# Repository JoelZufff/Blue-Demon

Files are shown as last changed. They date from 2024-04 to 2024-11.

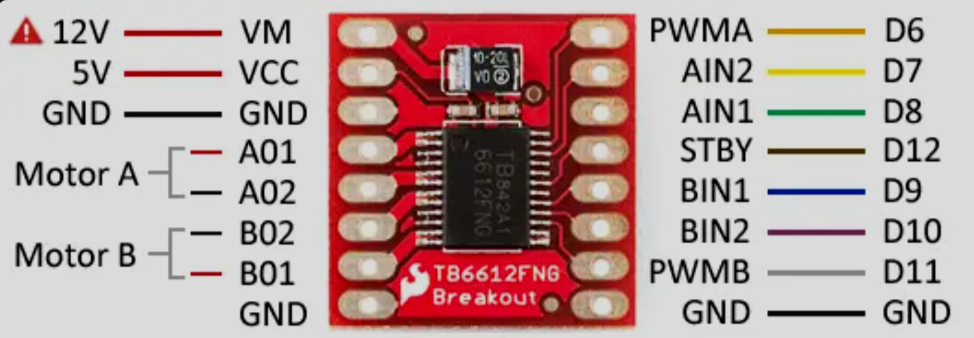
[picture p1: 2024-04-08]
Auxiliar-Files/HW-166.png

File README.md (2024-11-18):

**Robot para competencia Minisumo**
Este fue uno de mis proyectos más demandantes, ya que, además de las limitaciones de tamaño y peso de la competencia, todo se creó desde cero, sin comprar diseños preexistentes ni módulos de control preprogramados.

**Diseño:**  
Se diseñó de manera personalizada desde cero en el software SOLIDWORKS, teniendo en cuenta las restricciones de tamaño de la competencia.

- Se priorizó el máximo aprovechamiento del espacio, asegurando una distribución adecuada del peso para lograr un diseño estable.
- La carcasa fue impresa en 3D con filamento PETG de color azul. Se eligió este material por su mayor dureza en comparación con el PLA.
- La base fue fabricada en una placa de aluminio con la ayuda de un profesor, a partir de un modelo 3D.

**Programación de microcontrolador:**  
La programación se realizó utilizando PIC C COMPILER.

- Se configuraron los periféricos manipulando registros a través de punteros, obteniendo las direcciones de memoria de la hoja de datos del fabricante.
- Se implementó una codificación robusta y fácil de entender, aprovechando las herramientas del lenguaje C, como funciones selectivas, iterativas, estructuras y punteros.
- Se utilizaron **TIMERS** para generar 4 señales PWM y un timer con interrupción exclusivo para verificar la conexión con el control.
- Se empleó el protocolo de comunicación serial **RS232** para recibir las instrucciones del controlador.

**Programación de control:**  
Se desarrolló un programa en **C#** para Windows que actuó como intermediario entre el control y el robot Minisumo.

- Se aprovechó la compatibilidad del software para obtener la posición de los joysticks, botones y gatillos de un control de Xbox. Los datos obtenidos se organizaban en una cadena de caracteres siguiendo nuestro propio protocolo.
- Se utilizó un **TIMER** para enviar los datos recibidos del control a una tasa de 40 Hz. Estos datos se transmitían al microcontrolador del robot a través de Bluetooth utilizando el protocolo **RS232**.
- Los datos se enviaban a una tasa fija para que el microcontrolador pudiera detectar una desconexión cuando no se recibían datos en un periodo determinado.

**Componentes electrónicos:**  

- **Microcontrolador PIC 18F26K22**: Microcontrolador de 16 MHz con 5 módulos CCPX, lo que nos permitió generar 4 señales PWM independientes.
- **Módulo Bluetooth HC-05**: Módulo que facilitó la recepción de datos desde la computadora al microcontrolador mediante Bluetooth.
- **4 micromotorreductores de 150 rpm**: Motores con engranajes metálicos que ofrecieron un buen equilibrio entre torque y velocidad.
- **Regulador de voltaje L7805**: Acompañado de un condensador, ayudó a regular el voltaje de la batería para alimentar el microcontrolador.
- **Driver puente H TB6612FNG**: Driver eficiente para controlar los micromotores, capaz de trabajar a frecuencias más altas que los comunes L298N.
- **Batería de 2000 mAh a 7.4 V**: Batería para coches de radiocontrol, que cumplió con los requisitos de voltaje y corriente del sistema.

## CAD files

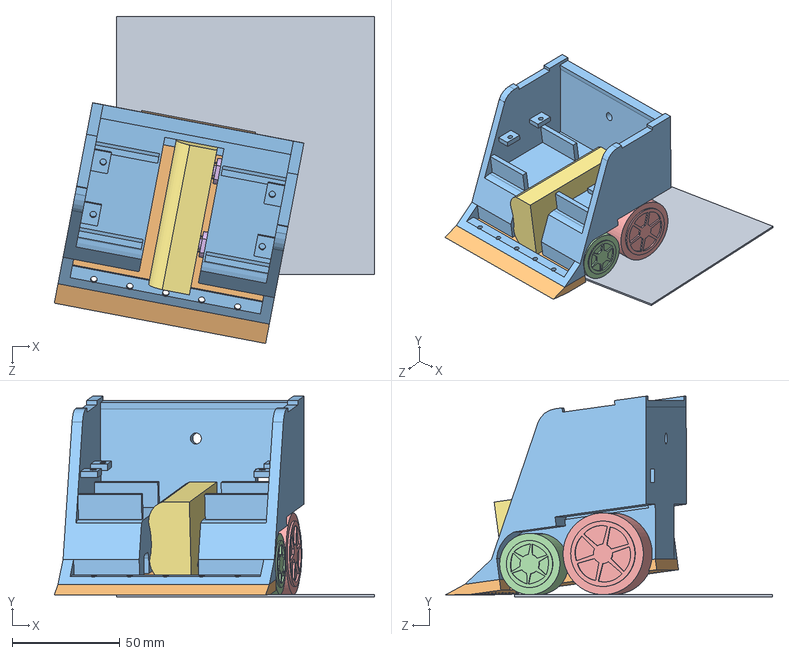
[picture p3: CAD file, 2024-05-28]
Diseño3D/EnsamblajeT.SLDASM
148.9 x 93.2 x 152.0 mm
pista
Base
Carcasanueva
RinCH
RinG
micromotor x 2
Bateria

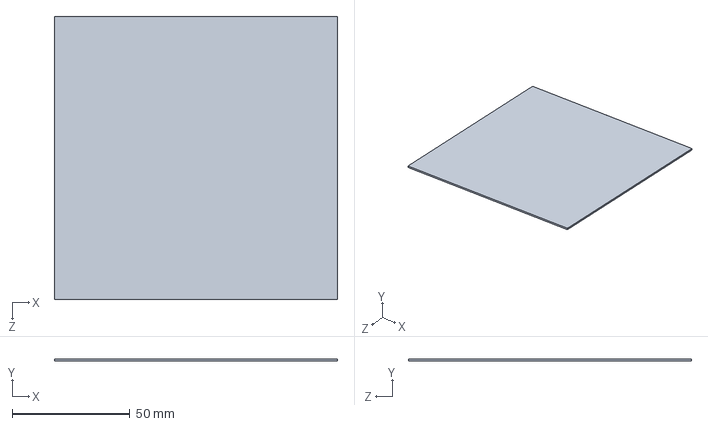
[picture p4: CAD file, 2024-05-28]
Diseño3D/pista.SLDPRT
120.0 x 1.00 x 120.0 mm

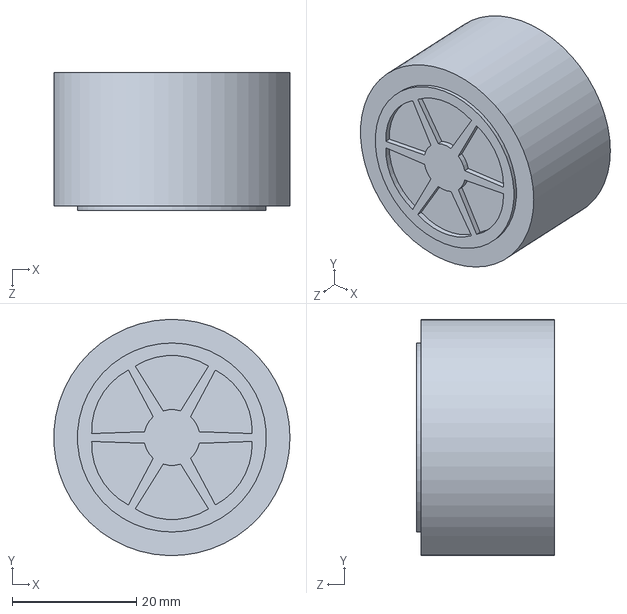
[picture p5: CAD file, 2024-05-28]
Diseño3D/RinG.SLDPRT
38.0 x 38.0 x 22.2 mm

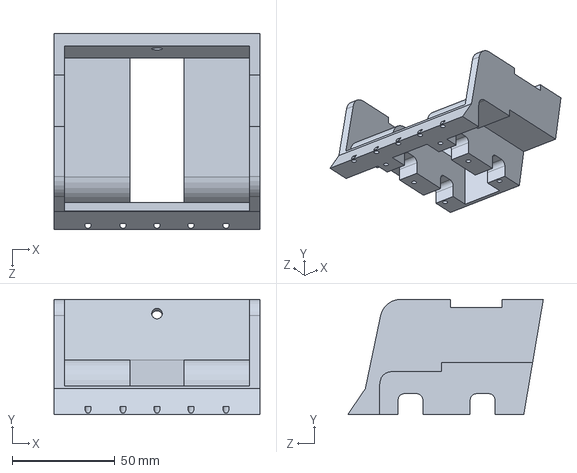
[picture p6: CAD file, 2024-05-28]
Diseño3D/Carcasanueva.SLDPRT
100.0 x 56.0 x 95.0 mm

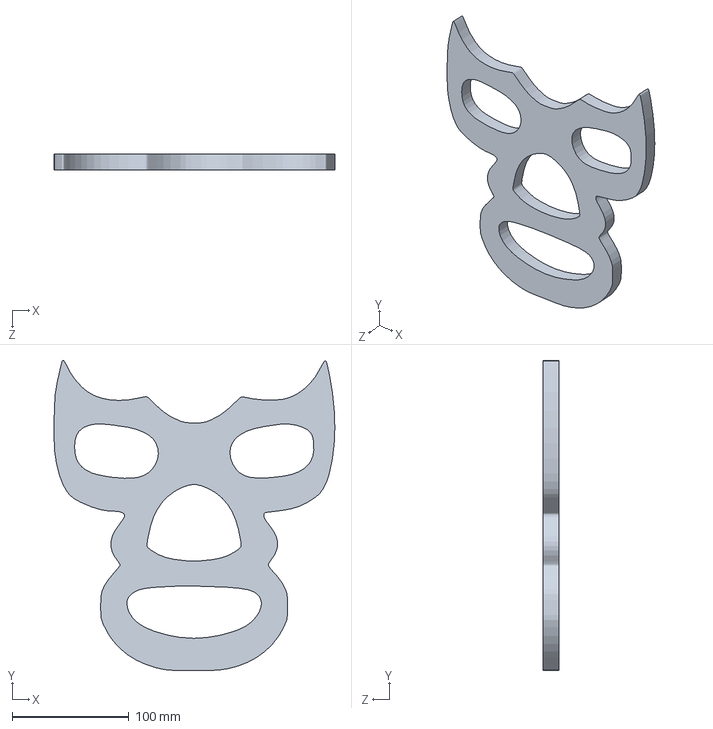
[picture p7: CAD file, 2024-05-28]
Diseño3D/DiseñoMascara.SLDPRT
240.2 x 265.3 x 13.3 mm

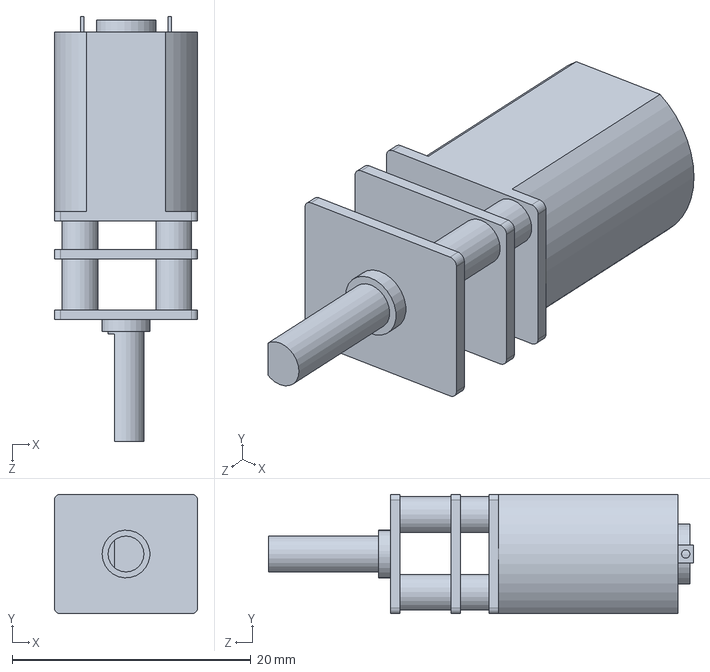
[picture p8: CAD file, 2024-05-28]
Diseño3D/micromotor.SLDPRT
12.0 x 10.0 x 35.6 mm

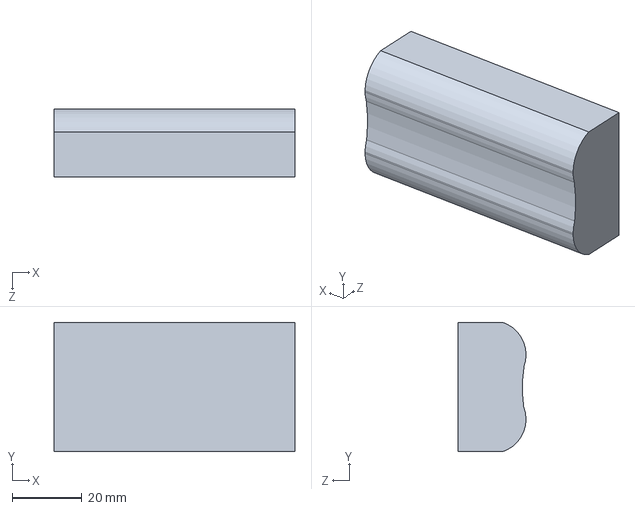
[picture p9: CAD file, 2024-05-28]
Diseño3D/Bateria.SLDPRT
69.0 x 37.0 x 19.5 mm

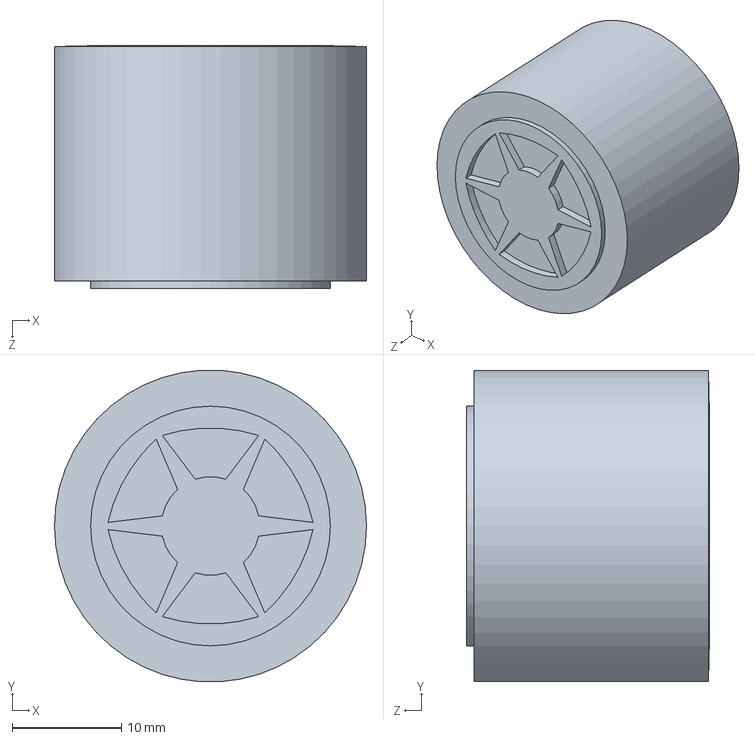
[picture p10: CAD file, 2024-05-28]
Diseño3D/RinCH.SLDPRT
28.5 x 28.4 x 22.2 mm

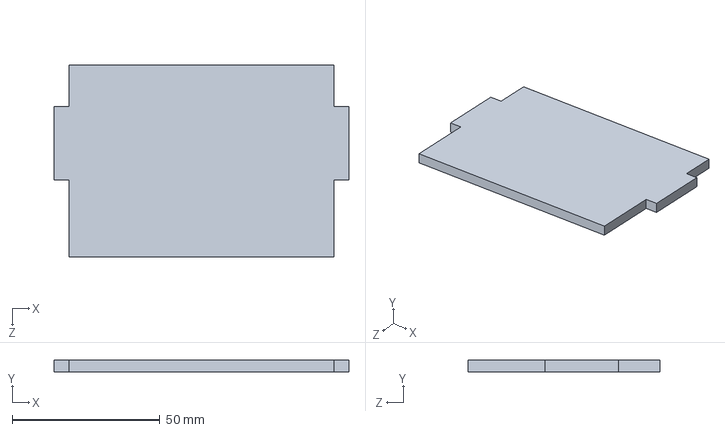
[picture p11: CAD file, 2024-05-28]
Diseño3D/Tapa_superior.SLDPRT
100.0 x 4.00 x 65.0 mm

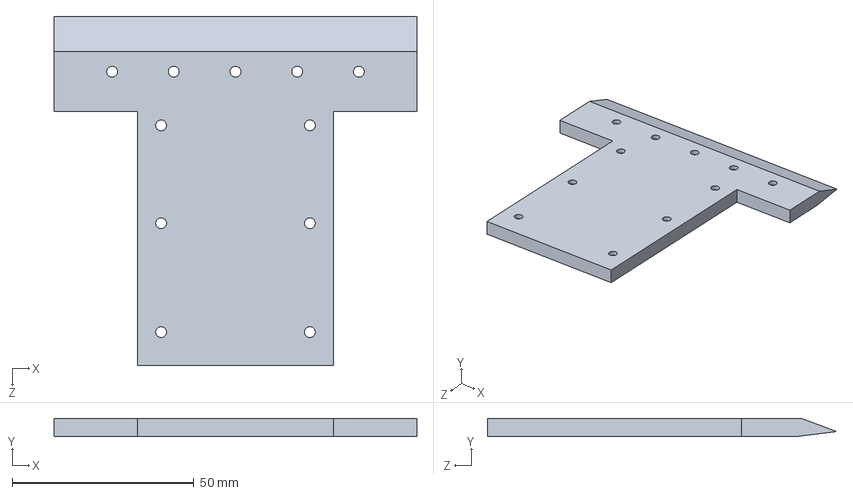
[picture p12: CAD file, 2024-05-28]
Diseño3D/Base.SLDPRT
100.0 x 5.02 x 96.3 mm

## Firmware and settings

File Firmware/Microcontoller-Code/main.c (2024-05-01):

// --------------- Preprocesadores de microcontrolador -------------- //
#include    <18F26K22.h>                                                // Libreria del Microcontrolador
#fuses      INTRC, NOWDT, NOPROTECT, NOLVP, NOMCLR, CCP2C1, CCP3B5      // Fusibles (Multiplexado de P2B en C0)
#use        delay(internal = 16MHz)                                     // Configuracion de frecuencia y delay
#use        rs232(rcv = pin_c7, xmit = pin_c6, baud = 9600, bits = 8, parity = n) 

#include    <stdlib.h>
#include    "motor_control.c"

// --------------------- Direccion de registros --------------------- //
#BYTE       TRISA               = 0xF92
#BYTE       TRISB               = 0xF93
#BYTE       TRISC               = 0xF94
#BIT        status_LED          = 0xF89.0   // LATA

#BYTE       INTCON              = 0xFF2
#BIT        INT1IE              = 0xFF0.3   // INTCON3

#BIT        INTEDG1             = 0xFF1.5   // INTCON2
#BIT        RC1IE               = 0xF9D.5   // PIE1
#BIT        IPEN                = 0xFD0.7   // RCON
#BIT        RC1IP               = 0xF9F.5   // IPR1

#BYTE       T0CON               = 0xFD5
#BIT        TMR0ON              = 0xFD5.7   // T0CON
const int16 *TMR0               = 0xFD6;
#BIT        TMR0IP              = 0xFF1.2   // INTCON2

// ----------------------- Variable Globales ------------------------ //
struct motor_t  tires[2][2]   = 
{
    {   // Llantas delanteras
        { 0xFBE, PIN_B3, PIN_B4 },  // Izquierda
        { 0xF67, PIN_B6, PIN_B7 }   // Derecha
    },
    {   // Llantas traseras
        { 0xF5E, PIN_A4, PIN_A5 },  // Izquierda
        { 0xF58, PIN_A6, PIN_A7 }   // Derecha
    }
};

struct          controller_t xbox_controller;
struct          bth_conection_t PC = { FALSE, FALSE };

// -------------------------- Interrupciones ------------------------ //
#INT_RDA
void control_instructions()
{
    int data = getch();
    
    if(data == '*')     // Recibimos caracter de inicio de datos
    {           
        char XJoystick[8], LeftTrigger[5], RightTrigger[5];
        
        // Obtenemos cadenas de caracteres con los valores a recibir
        gets(XJoystick);
        gets(LeftTrigger);
        gets(RightTrigger);

        // Realizamos la conversion y actualizamos los valores del control
        xbox_controller.JoystickX   =  atol(XJoystick);        
        xbox_controller.Triggers[0] =  atol(LeftTrigger);
        xbox_controller.Triggers[1] =  atol(RightTrigger);

        if(!PC.IsConnected)     // Si no habia conexion
            *TMR0 = 40535, TMR0ON = TRUE;

        // Actualizamos variables de conexion
        PC.updated_data = PC.IsConnected = PC.Check = TRUE;
    }
}

#INT_TIMER0
void connection_check()
{
    if(PC.Check)        // Hubo confirmacion de conexion
    {
        PC.Check = FALSE;       // Solicitamos nueva confirmacion
        *TMR0 = 40535;
    }
    else                // No hubo confirmacion de conexion
        PC.IsConnected = TMR0ON = FALSE;    // Desactivamos timer y booleano de conexion
}

/* Inforamcion de variables
* updated_data: Booleano para señalar que hubo una actualizacion de informacion y no ha sido aplicada.
    * updated_data = FALSE   : No hay nueva informacion
    * updated_data = TRUE    : Hay informacion pendiente de aplicar
* isConnected: Booleno para saber el estatus de la conexion de bluetooth
*/

// ---------------------------- Funciones --------------------------- //
void log_init()
{
    // Configuracion de pines GPIO
    TRISA       = 0b00000000;
    TRISB       = 0b00000010;
    TRISC       = 0b10000000;

    INTCON = 0b11100000;

    // Interrupcion de timer 0 para comprobar conexion
    T0CON = 0b00000011;     // 10 Hz
    *TMR0 = 40535;

    // Configuracion de Interrupciones
    IPEN = RC1IE = RC1IP =  TRUE;       // Establecemos la interrupcion de recepcion serial como prioridad
    TMR0IP = FALSE;
}

// ------------------------ Codigo Principal ----------------------- //
void main()
{
    log_init();
    motors_init(tires);

    Connection_animation:    
    // Esperamos conexion bluetooth con una animacion del LED indicador
    for(int time = 0; !PC.IsConnected; time++, delay_ms(1))
    {
        if(time == 200)
        {
            status_LED ^= TRUE;
            time = 0;
        }
    }

    status_LED = TRUE;      // Ya hubo conexion

    while (TRUE)
    {   
        //*/
        if(!PC.IsConnected)                 // Si se pierde la conexion
        {
            // Aplicamos freno de corto cuando no hay conexion
            motor_movement(&tires[0][0]), motor_movement(&tires[0][1]);
            motor_movement(&tires[1][0]), motor_movement(&tires[1][1]);
            
            goto Connection_animation;
        }

        // Si hay conexion
        if(PC.updated_data)                // Si se actualizo la posicion
        {
            // Enviamos instrucciones a motores
            drive_tires(&xbox_controller, tires);
            PC.updated_data = FALSE;
        }
        //*/

        /*/ Revision de  almacenamiento de variables
        printf("Joystick X = %ld | Y = %ld\r\n", xbox_controller.Joystick[0], xbox_controller.Joystick[1]);
        printf("Triggers 1 =  %u | 2 = %u\r\n", xbox_controller.Triggers[0],  xbox_controller.Triggers[1]);
        delay_ms(100);
        //*/
    }
}

/*
El codigo esta compuesto de las siguientes partes

    * Interrupcion de recepcion de datos en puerto serial: Recibe los datos actualizados del control de XBOX desde el programa de computadora en C#

    * Interrupcion de Timer 0: Se activa al detectar por primera vez la conexion, y monitorea la continuidad de la conexion

    * Funcion principal: Inicializa los registros, y mueve las ruedas cuando hay nueva informacion
*/

// Falta hacer interrupcion cada 150 ms para revisar conexion y corregir no llegar a velocidad maxima con 2 llantas por falta de precision de joystick, ademas de eliminar la lectura de joystick en Y.

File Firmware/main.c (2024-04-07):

// --------------- Preprocesadores de microcontrolador -------------- //
#include    <18F26K22.h>                                                // Libreria del Microcontrolador
#fuses      INTRC_IO, NOWDT, NOPROTECT, NOLVP, NOMCLR, CCP2C1, CCP3C6   // Fusibles (Multiplexado de P2B en C0)
#use        delay(internal = 16MHz)                                     // Configuracion de frecuencia y delay
//#use        rs232(rcv = pin_b7, xmit = pin_b6, baud = 9600, bits = 8, parity = n) 

#define RIGHT   1
#define LEFT    0

// --------------------- Direccion de registros --------------------- //
#BYTE       TRISA           = 0xF92
#BYTE       TRISB           = 0xF93
#BYTE       TRISC           = 0xF94
#BIT        BUTTON          = 0xF80.1

const int16 *ADRES          = 0xFC3;
#BYTE       ADCON0          = 0xFC2
#BIT        DONE            = 0xFC2.1
#BYTE       ADCON2          = 0xFC0

#BYTE       CCPTMRS0        = 0xF49
#BYTE       CCPTMRS1        = 0xF48

#BYTE       CCP1CON         = 0xFBD
#BYTE       CCP2CON         = 0xF66
#BYTE       CCP3CON         = 0xF5D
#BYTE       CCP4CON         = 0xF57

#BYTE       T2CON           = 0xFBA
#BYTE       PR2             = 0xFBB

// -------------------------- Estructuras --------------------------- //
struct wheel_t
{
    int     *DutyCicle;
    long    in_pins[2];
};

// ----------------------- Variable Globales ------------------------ //
struct wheel_t wheels[4] = 
{
    { 0xFBE, { PIN_B1, PIN_B2 } },  /* Rueda A */ 
    { 0xF67, { PIN_B3, PIN_B4 } },  /* Rueda B */
    { 0xF5E, { PIN_B5, PIN_B6 } },  /* Rueda C */
    { 0xF58, { PIN_C3, PIN_C4 } }   /* Rueda D */
};

// -------------------------- Interrupciones ------------------------ //


// ---------------------------- Funciones --------------------------- //
void log_init()
{
    // Configuracion de pines GPIO
    TRISA       = 0b00000011;
    TRISB       = 0b00000000;
    TRISC       = 0b00000000;

    // Configuracion de ADC
    ADCON0      = 0b00000011;
    ADCON2      = 0b10000000;

    // Configuracion de Timers
    T2CON       = 0b00000111;
    PR2         = 249;
    
    // Configuracion de CCPXCON para PWM
    CCPTMRS0 = CCPTMRS0 = 0b00000000;       // Configuramos CCPX con timer 2
    CCP1CON = CCP2CON = CCP3CON = CCP4CON = 0b00001100;
}

void wheel_movement(int wheel_index, int1 direction)
{
    output_bit(wheels[wheel_index].in_pins[0], direction);
    output_bit(wheels[wheel_index].in_pins[1], !direction);
}

// ------------------------ Codigo Principal ----------------------- //
void main()
{
    log_init();

    int1 direction = LEFT;
    int16 ADC;

    for(int i = 0; i < 4 ; i++)
        wheel_movement(i, direction);

    while (TRUE)
    {
        ADCON0  = 0b00000011;
        delay_us(10);
        ADC = (*ADRES / 1023.0 * 1000);
        
        for(int i = 0; i < 4 ; i++)
            (wheels[i])->DutyCicle = ADC >> 2;

        if(BUTTON)
        {
            while(BUTTON);
            direction ^= 1;
            
            wheel_movement(0, direction);
            wheel_movement(1, direction);
            wheel_movement(2, direction);
            wheel_movement(3, direction);
        }
    }
}

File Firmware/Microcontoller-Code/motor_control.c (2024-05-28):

#define     FORWARD     1
#define     BACK        0

#define     max_dutycicle       320
#define     min_dutycicle       max_dutycicle / 15

#define     max_trigger_value   255
#define     max_joystick_value  32767.0
#define     min_joystick_value  1200

// -------------------- Direcciones de registros -------------------- //
#BYTE       CCPTMRS0        = 0xF49
#BYTE       CCPTMRS1        = 0xF48

#BYTE       CCP1CON         = 0xFBD
#BYTE       CCP2CON         = 0xF66
#BYTE       CCP3CON         = 0xF5D
#BYTE       CCP4CON         = 0xF57

#BYTE       T2CON           = 0xFBA
#BYTE       PR2             = 0xFBB

// -------------------------- Estructuras --------------------------- //
struct bth_conection_t
{
    short updated_data;
    short IsConnected;
    short Check;
};

struct motor_t
{
    int     *DutyCicle;
    long    IN1_pin;
    long    IN2_pin;
};

struct controller_t
{
    signed long         JoystickX;      // Entero de -32768 a 32767 (0 eje x, 1 eje y)
    int                 Triggers[2];    // Entero de 0 a 255 (0 izquierdo, 1 derecho)
};

// ---------------------------- Funciones --------------------------- //
void motors_init(struct motor_t tires[2][2])
{
    // Configuracion de Timers
    T2CON       = 0b00000100;
    PR2         = 79;
    
    // Configuracion de CCPXCON para PWM
    CCPTMRS0 = CCPTMRS0 = 0b00000000;       // Configuramos CCPX con timer 2
    
    // Configiracion de modulo CCPX para PWM
    CCP4CON = 0b00001100, CCP3CON = 0b00001100, CCP2CON = 0b00001100, CCP1CON = 0b00001100;

    for(int i = 0; i < 2 ; i++)
        for(int j = 0; j < 2; j++)
            *(tires[i][j].DutyCicle) = 0;
}

void motor_movement(struct motor_t *motor, float speed)   // Modo de movimiento normal
{
    short direction = (speed >= 0) ? FORWARD : BACK;
    
    // Establecemos direccion de giro
    output_bit(motor->IN1_pin, direction);
    output_bit(motor->IN2_pin, !direction);
    
    // Establecemos DC para velocidad
    long aux = ((max_dutycicle - min_dutycicle) * abs(speed) / 100) + min_dutycicle;
    *(motor->DutyCicle) = aux >> 2;
}

void motor_movement(struct motor_t *motor)    // Modo de freno de corto (Solo para emergencias)
{
    output_high(motor->IN1_pin);
    output_high(motor->IN2_pin);
}

void drive_tires(struct controller_t *xbox_controller, struct motor_t tires[2][2])
{    
    // Si estan presionados los 2 al maximo, aplicamos freno de corto y salimos de funcion
    if((xbox_controller->Triggers[0] == 255) && (xbox_controller->Triggers[1] == 255))
    {
        // Activamos modo short brake
        motor_movement(&tires[0][0]), motor_movement(&tires[0][1]);
        motor_movement(&tires[1][0]), motor_movement(&tires[1][1]);
        return;
    }
    
    /*  Notas para comprender
    * Llanta contraria al giro, avanza con normalidad a la velocidad indicada (speed)
    * Llanta de apoyo, gira a menor velocidad en funcion de que tan desviado hacia la direccion esta el joystick 
        ∵ (-speed < turning_speed < speed)
    */

    // Si no se aplico freno de corto, calculamos velocidad y direccion de movimiento
    
    float speed[2];
    
    if((xbox_controller->Triggers[0] == 0) && (xbox_controller->Triggers[1] == 0))
    {
        // Giro en propio eje

        if(xbox_controller->JoystickX > 15000)        // El movimiento es a la derecha
        {
            speed[0] = 50;
            // Flotante de -100 a 100 que indica la velocidad y direccion de movimiento (+ adelante, - atras)
            speed[1] = -50;
            // Velocidad - (Velocidad * (Valor Joystick X / Valor maximo Joystick X))
        }
        else if(xbox_controller->JoystickX < -15000)   // El movimiento es a la izquierda
        {
            speed[1] = 50;
            // Flotante de -100 a 100 que indica la velocidad y direccion de movimiento (+ adelante, - atras)
            speed[0] = -50;
            // Velocidad - (Velocidad * (Valor Joystick X / Valor maximo Joystick X))
        }
        else        // El movimiento es recto
            speed[0] = speed[1] = 0;
            // Flotante de -100 a 100 que indica la velocidad y direccion de movimiento (+ adelante, - atras)
    }
    else
    {
        signed long trigger_diff = (signed long) xbox_controller->Triggers[1] - xbox_controller->Triggers[0];

        if(xbox_controller->JoystickX > min_joystick_value)        // El movimiento es a la derecha
        {
            speed[0] = trigger_diff * 100.0 / max_trigger_value;
            // Flotante de -100 a 100 que indica la velocidad y direccion de movimiento (+ adelante, - atras)
            speed[1] = speed[0] - (speed[0] * (xbox_controller->JoystickX - min_joystick_value) / (max_joystick_value - min_joystick_value));
            // Velocidad - (Velocidad * (Valor Joystick X / Valor maximo Joystick X))
        }
        else if(xbox_controller->JoystickX < -min_joystick_value)   // El movimiento es a la izquierda
        {
            speed[1] = trigger_diff * 100.0 / max_trigger_value;
            // Flotante de -100 a 100 que indica la velocidad y direccion de movimiento (+ adelante, - atras)
            speed[0] = speed[1] - (speed[1] * (xbox_controller->JoystickX + min_joystick_value) / (-32768.0 + min_joystick_value));
            // Velocidad - (Velocidad * (Valor Joystick X / Valor maximo Joystick X))
        }
        else        // El movimiento es recto
            speed[0] = speed[1] = trigger_diff * 100.0 / max_trigger_value;
            // Flotante de -100 a 100 que indica la velocidad y direccion de movimiento (+ adelante, - atras)
    }

    // Enviamos movimiento a las llantas //
    motor_movement(&tires[0][0], speed[0]);      // Llanta delantera izquierda
    motor_movement(&tires[1][0], speed[0]);      // Llanta trasera izquierda
    
    motor_movement(&tires[0][1], speed[1]);      // Llanta delantera derecha
    motor_movement(&tires[1][1], speed[1]);      // Llanta trasera derecha
}

/*
Los gatillos establecen la velocidad maxima de giro, y la posicion del joystick establece como se repartira esta velocidad en las llantas, para poder hacer diferentes maniobras, por ejemlo:

* Cuanto mas pegado al maximo o minimo del eje Y, mayor sera la diferencia de velocidad entre las llantas de la izquierda con las de la derecha
* Cuanto mas pegado al maximo o minimo del eje X, mayor sera la diferencia de velocidad entre las llantas de arriba y abajo

Por lo tanto: 
* La llanta mas lejana a la direccion de movimiento en X tendra mas velocidad que la mas pegada
* La llanta mas lejana a la direccion de movimiento en Y tendra mas velocidad que la mas pegada
*/ 

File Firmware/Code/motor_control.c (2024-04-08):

#define     max_dutycicle   160

// -------------------- Direcciones de registros -------------------- //
#BYTE       CCPTMRS0        = 0xF49
#BYTE       CCPTMRS1        = 0xF48

#BYTE       CCP1CON         = 0xFBD
#BYTE       CCP2CON         = 0xF66
#BYTE       CCP3CON         = 0xF5D
#BYTE       CCP4CON         = 0xF57

#BYTE       T2CON           = 0xFBA
#BYTE       PR2             = 0xFBB

// -------------------------- Estructuras --------------------------- //
struct motor_t
{
    int     *DutyCicle;
    long    IN1_pin;
    long    IN2_pin;
};

// ---------------------------- Funciones --------------------------- //
void motors_init(int number)
{
    // Configuracion de Timers
    T2CON       = 0b00000100;
    PR2         = 39;
    
    // Configuracion de CCPXCON para PWM
    CCPTMRS0 = CCPTMRS0 = 0b00000000;       // Configuramos CCPX con timer 2
    
    switch (number)
    {
        case 4:
            CCP4CON = 0b00001100;
        case 3:
            CCP3CON = 0b00001100;
        case 2:
            CCP2CON = 0b00001100;
        case 1:
            CCP1CON = 0b00001100;
        break;
        default: break;
    }
}

/*  Donde:
* direcition    := Booleano para escoger derecha o izquierda
* speed         := Numero flotante de 0 a 100
*/
void motor_movement(struct motor_t motor, short direction, float velocity)
{
    // Establecemos direccion de giro
    output_bit(motor.IN1_pin, direction);
    output_bit(motor.IN2_pin, !direction);

    // Establecemos DC para velocidad
    long aux = max_dutycicle * velocity;  
    motor->DutyCicle = aux >> 2;
}

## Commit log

2024-03-25 Programacion: Configuracion de 3 PWM con complementarios
    [base.SLDPRT, micromotor.SLDPRT]
2024-03-28 Diseño 3D: Agregue BASE y LLANTAS TRASERAS
    [BASE.SLDPRT, LLANTA-TRASERA.SLDPRT, base.SLDPRT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]
2024-04-07 Firmware: Agregue movimiento de llantas con puente H
    [BASE.SLDPRT, Micro-motorreductor.SLDASM, Terreneitor.SLDASM]
2024-04-08 Firmware: Mejore organizacion y cree funciones para movimiento de motor con el modulo HW-166
2024-04-09 Firmware: Agregue codigo para mandar instrucciones de control de XBOX utilizando XInput
2024-04-13 Firmware: Agregue estructuras y funciones para movimiento de ruedas por instrucciones de control de xbox, ademas agregue programa en C# como intermediario para recepcion y envio de instrucciones de c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
    [BASE.SLDPRT, LLANTA-TRASERA.SLDPRT, Micro-motorreductor.SLDASM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]
2024-04-15 Firmware: Mejore conexion bluetooth y funciones de movimiento para ruedas
2024-04-16 Firmware: Corregi movimiento de motor y conexion bluetooth
2024-04-26 Firmware: Version Final
    [RinCHmod.STL, RinGmod.STL]
2024-05-28 VERSION 1 FINAL
    [Base.SLDPRT, Bateria.SLDPRT, Carcasanueva.SLDPRT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]
